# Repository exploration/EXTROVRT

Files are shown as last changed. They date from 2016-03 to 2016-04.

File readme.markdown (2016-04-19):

# EXTROVRT
([EXplo](http://www.explo.org) Telepresence RObot Via the inteRneT)

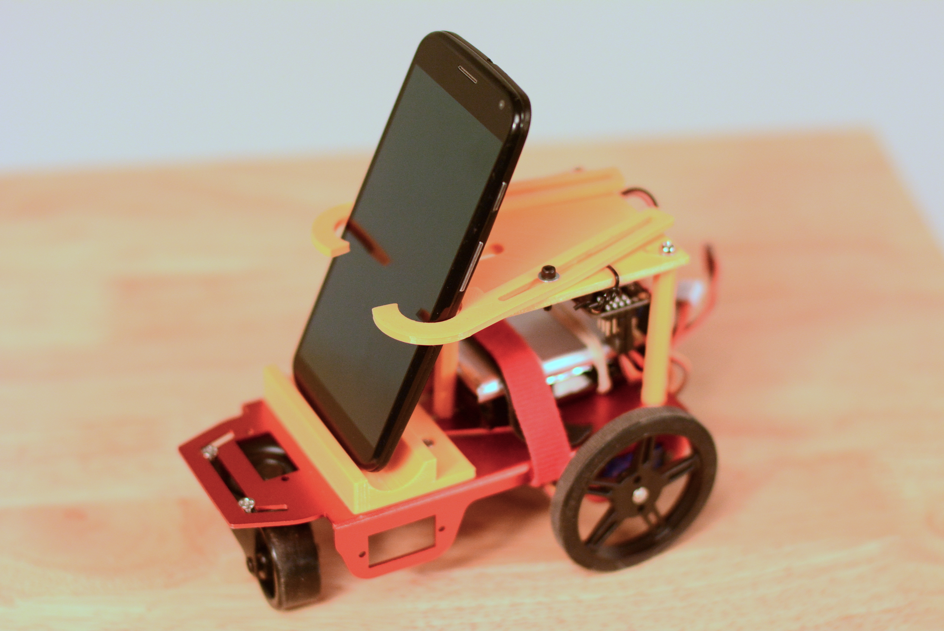
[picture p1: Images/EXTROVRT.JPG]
Glamour shot of the EXTROVRT robot


(more photos in the [Images](Images/) directory)

## What Is It?
EXTROVRT is a telepresence robot controlled via [Adafruit IO](http://adafruit.io)'s MQTT service, which uses [Adafruit Feather](https://www.adafruit.com/categories/777) stuff: the [Feather Huzzah ESP8266](https://www.adafruit.com/products/2821) and [Servo Featherwing](https://www.adafruit.com/products/2928) as the main control boards. We also have a [custom control interface](https://github.com/exploration/EXTROVRT-Control) written in Sinatra which lets us use the keyboard to drive instead of the mouse.

EXTROVRT came about because we have a [Double Robot](http://www.doublerobotics.com/) which was given to us, which we love and is a real hoot. However, it was going to require a brand-new iPad to upgrade. We figured that we could achieve 90% of the functionality of a Double for about 5% of the cost. We set the goal of a robot that could drive around using commodity servo hardware, and hold a phone, iPod touch, iPad, or the like. This would allow us to "turn our head" in virtual meetings, and even drive around a bit, probably mostly on tables.

We've achieved our goal! You should be able to make this robot for about $100, give or take.

This approach also has the benefit of allowing us to use whichever phone/tablet, and whichever video chat client (Skype, Google Hangouts, HipChat Video, etc) works best at the moment. We can also more easily test accessories like camera lenses or microphones.

## How Does It Work?
**Note:** If you want multiple EXTROVRTs, you might want to check out our [control software](https://github.com/exploration/EXTROVRT-Control) for more detailed setup instructions to make that work.

If you just want one robot, you can pretty easily set up the Adafruit IO interface. The way that works is this: You [set up a feed](https://learn.adafruit.com/adafruit-io-basics-feeds/overview) on [Adafruit IO](http://adafruit.io) as such:

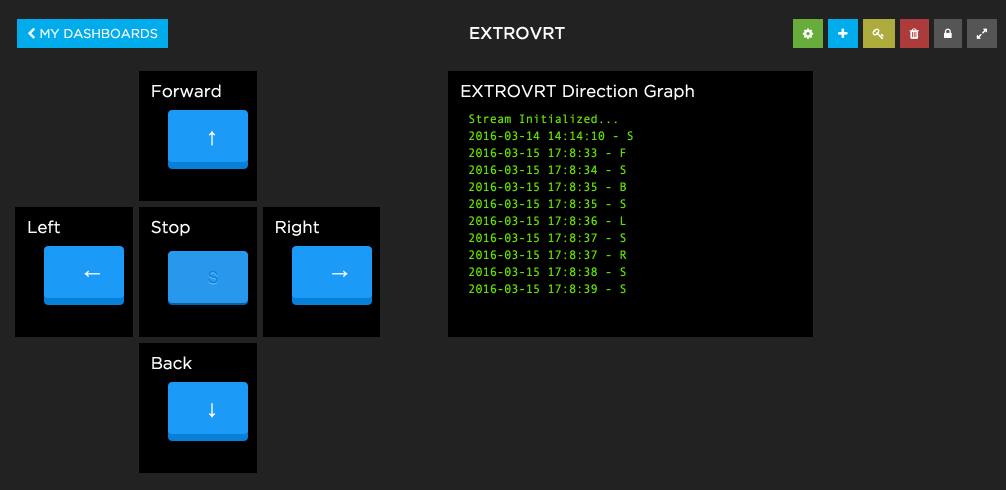
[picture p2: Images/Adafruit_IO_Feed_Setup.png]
Adafruit IO Feed Setup - Buttons with "F","B","L","R", and "S" values


Each button then gets mapped to a simple value: `F` for `Forward`, `B` for `Back`, `R` for `Right`, `L` for `Left`, and `S` for `Stop`. Each button is set up to send `S` when it is let go:

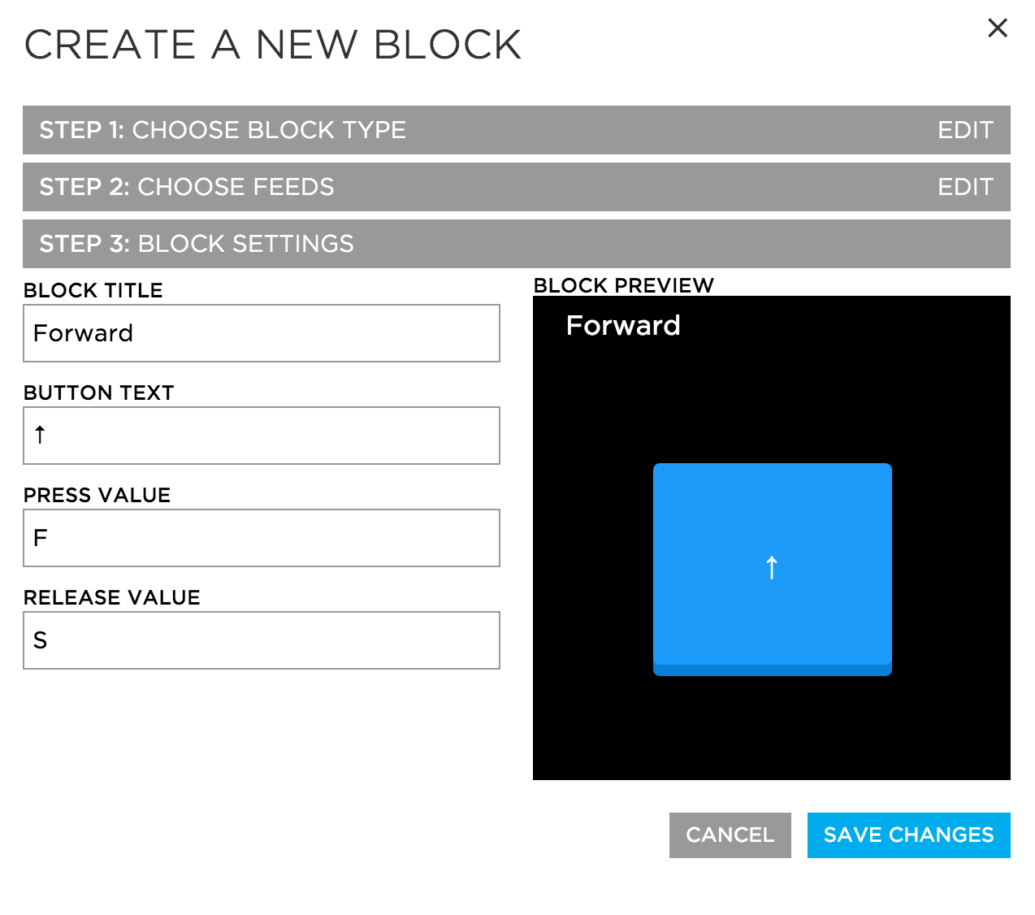
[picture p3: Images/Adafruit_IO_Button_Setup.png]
Adafruit IO Button Setup


For your initial setup, you may want to tweak the motor parameters so that max/min speed correspond to the "threshold" points of your servo motors. In that case, you should put in a "text" block so you can send the `MINUP`,`MINDOWN`,`MAXUP`,`MAXDOWN`,`STOPUP`, and `STOPDOWN` commands to the device. Make sure to record the motor values that work for you and hard-code them into the sketch so you won't have to adjust them every time you reset the device!

The Huzzah ESP8266 board will connect to your wifi, then connect to your Adafruit IO feed using [MQTT](https://learn.adafruit.com/mqtt-adafruit-io-and-you/overview). It monitors the feed for changes in direction, and sends motor information to the servos through the servo board. In practice, this all happens very darned close to real-time: close enough to work great! Until you hit the Adafruit IO API limit :/ But for the price of free, who's complaining?

## How Do I Build It?
### Parts + Assembly
You can get all of the parts for EXTROVRT at this [wishlist](https://www.adafruit.com/wishlists?wid=391765) here.

Physically, the entire robot is built around [this anodyzed aluminum chassis](https://www.adafruit.com/products/2943), two continuous-rotation micro servos with matching wheels, and a swivel-wheel for the front. The parts that hold the phone/tablet are all 3d-printed and bolted on (see below for details).

### Power
You need a battery source that's 5V and capable of handling something in the range of 500mA of current at 5V - 2.5 watts of power. The easiest way to accomplish this is to use a simple [USB Battery Pack](https://www.adafruit.com/products/1959) such as you might use for charging a phone, plugged right into the Feather Huzzah! You'll need to connect the `USB` and `GND` pins to the `+` and `-` screw terminals from the Adafruit Servo Wing to forward the power from USB to the servos (see power draw notes below).

You could alternately use an RC LiPo battery, or a simple 4xAA battery holder - anything is fine, but for this to work you'll have to connect a [UBEC](https://www.adafruit.com/products/1385) (buck converter) to the `USB` and `GND` pins on the Adafruit Feather, as well as the `+` and `-` pins from the Adafruit Servo Wing (the screw terminals) to get a stable 5 volt power source for the devices. Then connect your battery configuration to the other end of the UBEC.

(As an aside about power draw, my testing showed that the Huzzah draws about a continuous 0.05A or 50mA while idle, and the servos both running (normal speed) draws about 0.35A or 350mA. I imagine even if you maxed out the speed of these mini-servos, you'd still be within the 500mA spec of USB, let alone the spec of what a 7.2V 2S RC LiPo battery could attain.)

On my particular robot, I opted for a 2S (~7.3V) LiPo battery instead of the 4xAA holder, but that's only because I have those batteries (and and UBEC, and chargers) lying about from other projects. If you have RC batteries, you may prefer to use those, but most people will probably be happiest with just using a USB battery pack, since those are the most re-usable for other purposes when you're not EXTROVRT'ing.

### Wiring
Electronics-wise, you plug the servo "wing" on top of the Feather Huzzah! As noted above, you want to connect the `USB` and `GND` pins on the Adafruit Feather to the `+` and `-` pins from the Adafruit Servo Wing (the screw terminals) (and also to the 5V output of the UBEC if you're using one). On my devices, I install a power switch between the UBEC and the electronics so that I don't have to unplug any cables to turn the thing on + off.

### Arduino
The Arduino files are in the `Arduino` folder of this repository. You simply have to modify them to match your WiFi network SSID/password, and your particular Adafruit IO feed information. If you don't know how to upload Arduino code to the board, [this tutorial](https://learn.adafruit.com/adafruit-feather-huzzah-esp8266/overview) is exceedingly helpful.

### 3D Printing
Everything that's orange in the pictures is a 3d-printed thing. You'll need to print your own copy of those. You want two of the "arms", one top plate, and one base.

The CAD sources for the 3D-printed files are publicly available at [OnShape](https://cad.onshape.com/documents/d73cca1ae031f4b278264cff/w/0abe2b13ef53c6019a28a62a), which is handy if you want to fiddle with the models for your own setup.

I've also included the STL models and the [Simplify3D](https://www.simplify3d.com/) print setup files for a [PrintrBot Simple Metal](http://printrbot.com/shop/assembled-simple-metal/) in the `Models` and `Print Setup` folders, if you've got the same setup as me or use Simplify3D and want a starting point. I was able to print the entire thing within one 150mm square build plate.

I also had some luck making my own 3d-printed [Hex Standoffs](https://cad.onshape.com/documents/a721d24ec3e00633c0a5e028/w/56f9fc784b3159de2bad2fdf/e/3c67c912763ba927c46253c3), which is one fewer part you have to purchase if you have your own printer. Yes, I used imperial bolts (4/40) for that particular one, because I ran out of nice metric ones. But they should work with M3 bolts as well. And once again, it's OnShape, so it's easy to go + change dimensions and make your own - the model is fully parametric. You should be able to print them sideways on your build plate - it worked fine for me with no supports.

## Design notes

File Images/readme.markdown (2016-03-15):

Front
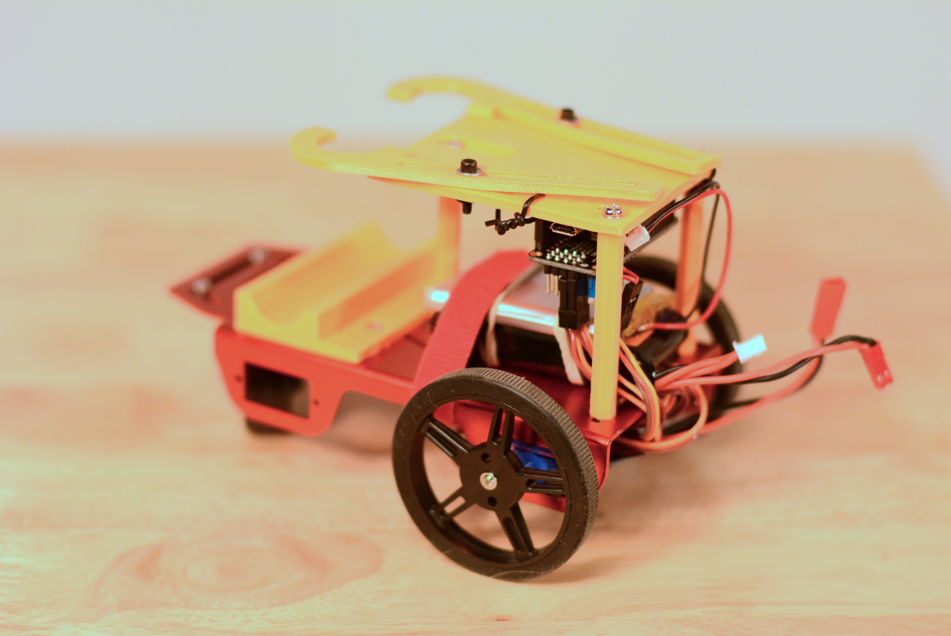
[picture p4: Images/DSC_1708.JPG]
Back Left Corner View

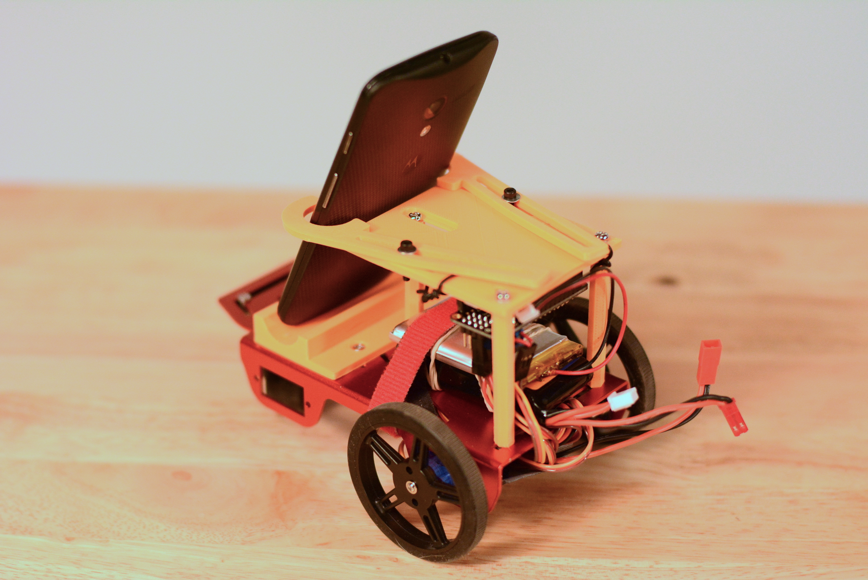
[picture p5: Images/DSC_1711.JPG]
Back Left with Phone View

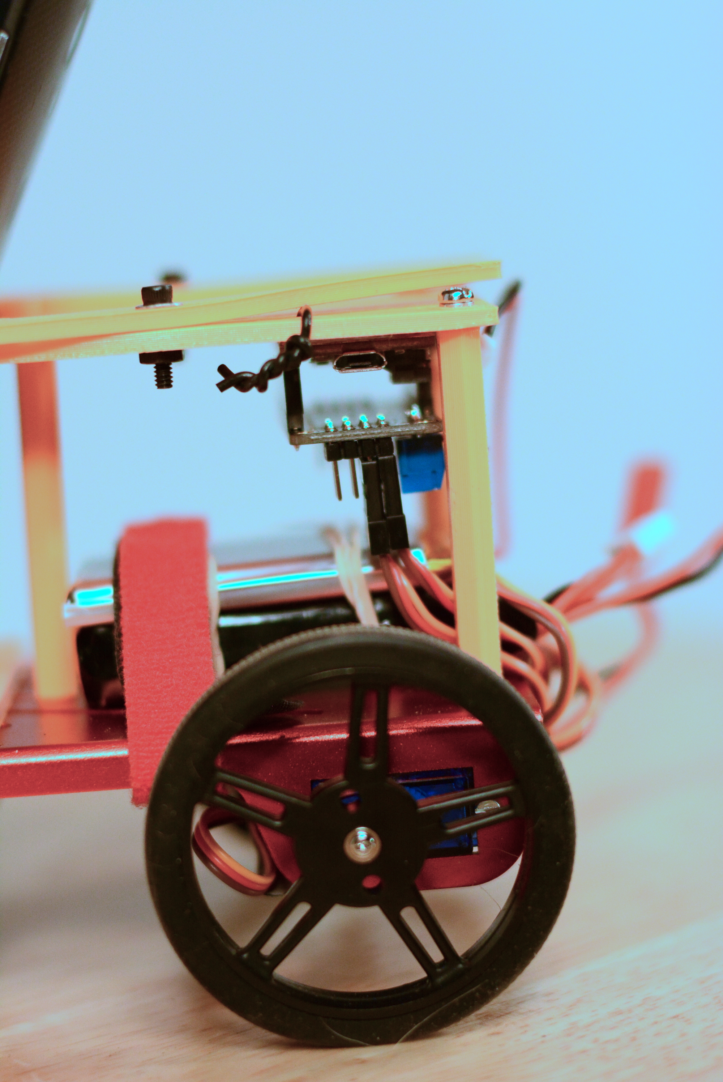
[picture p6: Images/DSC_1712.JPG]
Electronics Detail

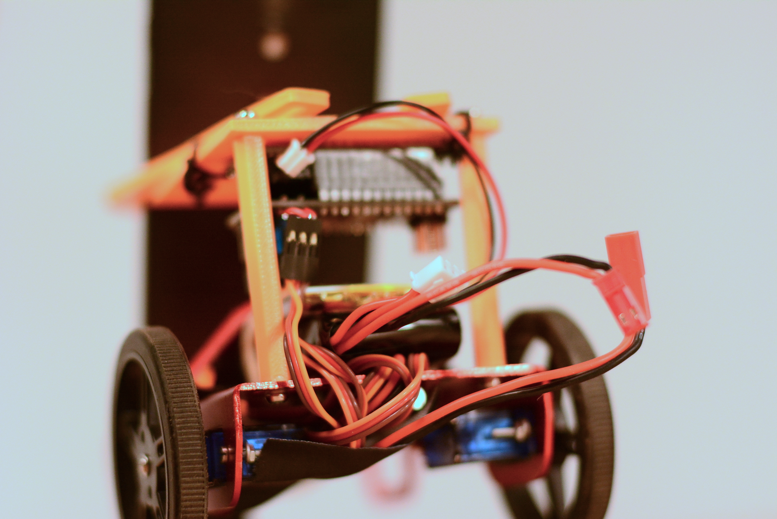
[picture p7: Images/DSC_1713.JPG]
Rear View

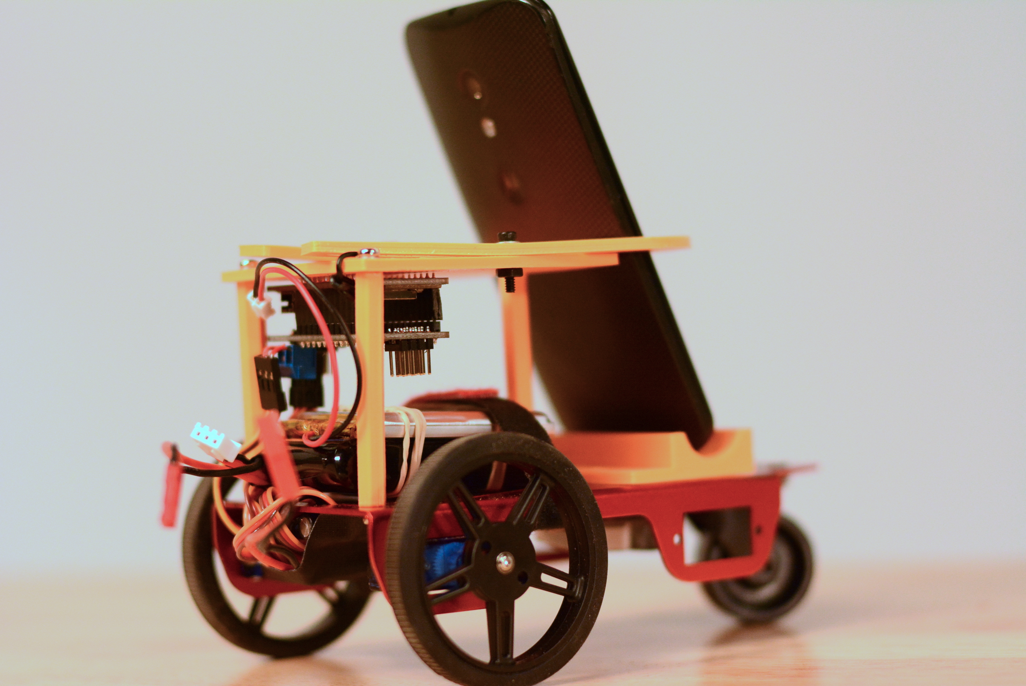
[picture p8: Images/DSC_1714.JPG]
Back Right View

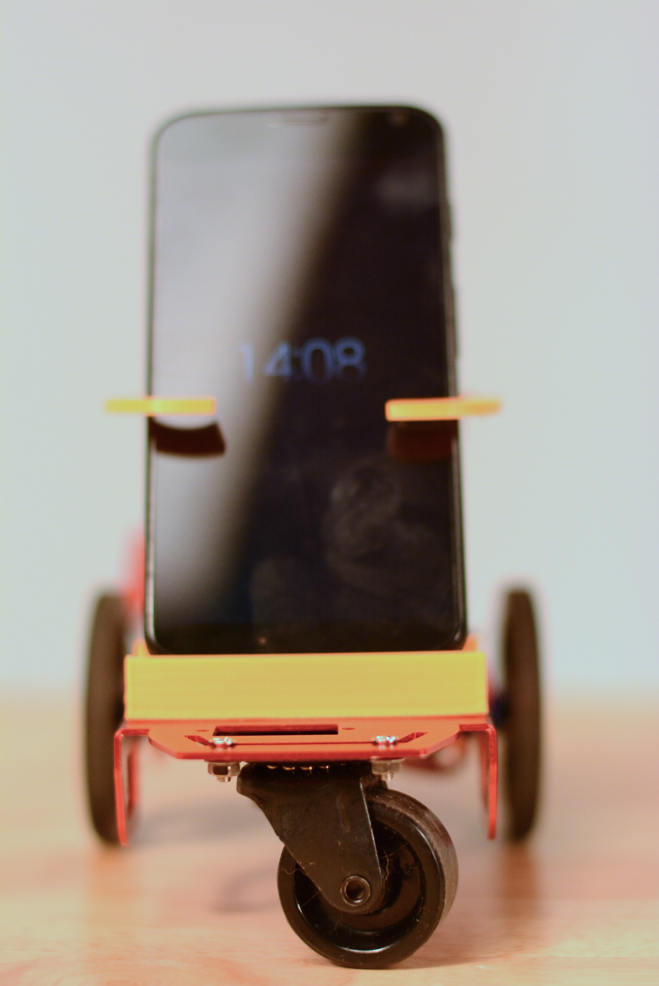
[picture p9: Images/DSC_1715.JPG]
Front View

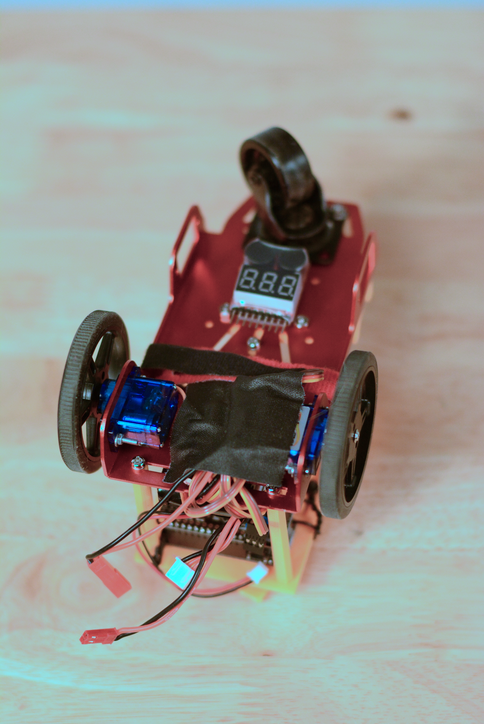
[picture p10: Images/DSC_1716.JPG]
Bottom View


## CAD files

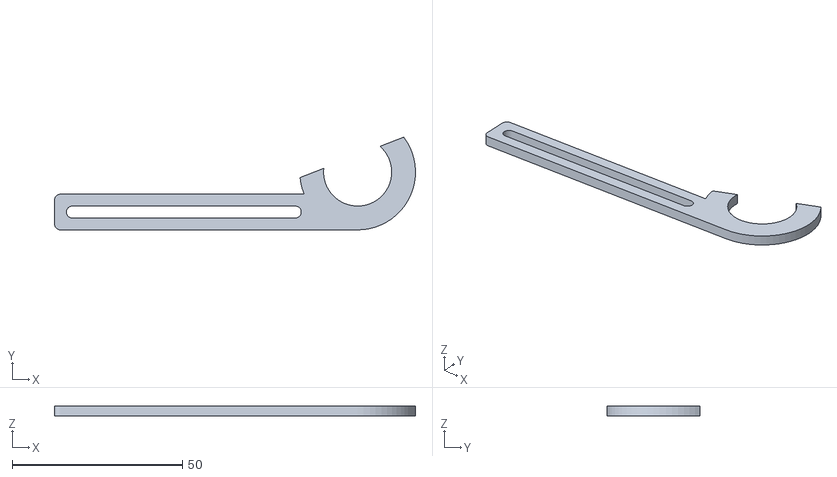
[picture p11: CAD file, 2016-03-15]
Models/iOS Device Robot Mount v2 - Arm.stl
106.1 x 27.3 x 3.00

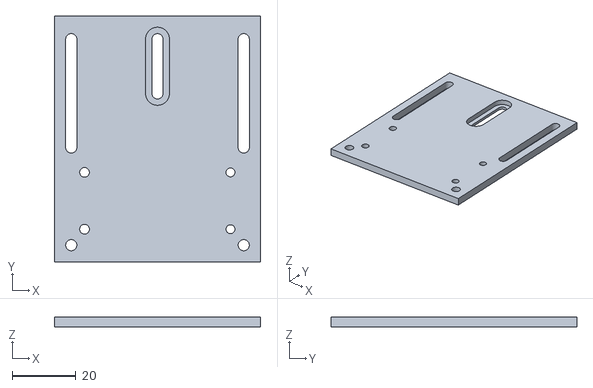
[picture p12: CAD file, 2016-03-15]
Models/iOS Device Robot Mount v2 - Top Plate.stl
64.5 x 77.0 x 3.00

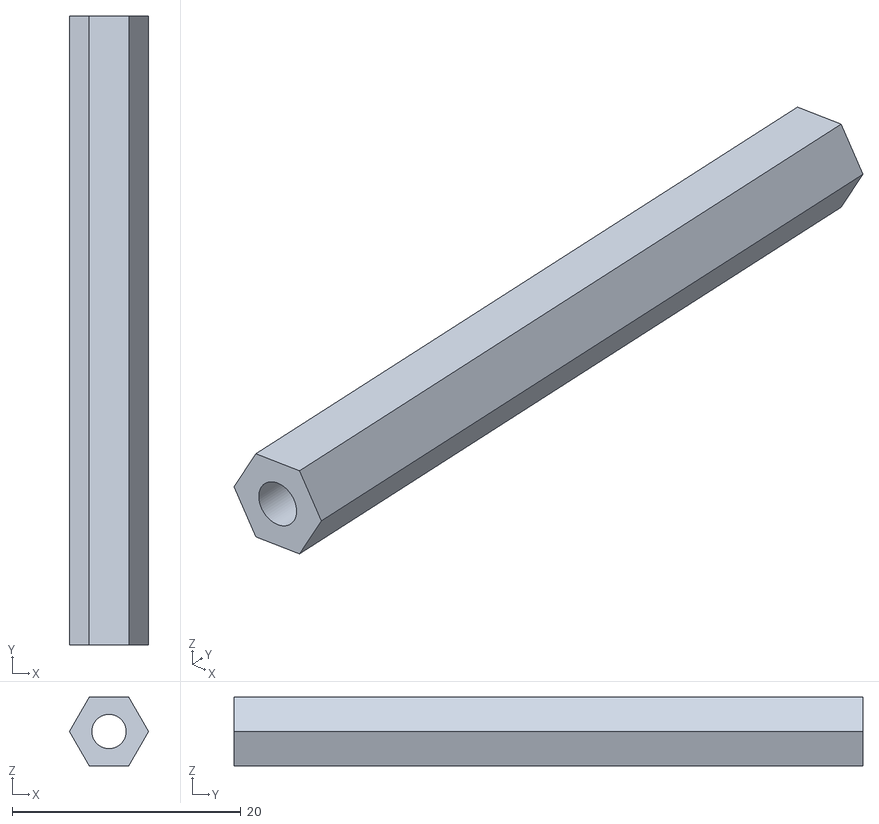
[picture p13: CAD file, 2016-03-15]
Models/Hex Standoff - 4-40 x 1-.stl
6.93 x 55.0 x 6.00

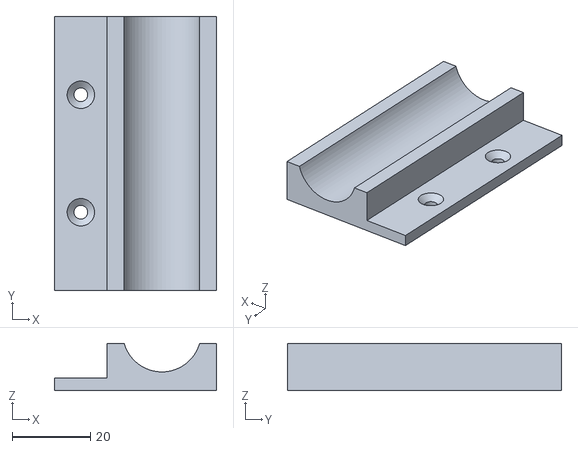
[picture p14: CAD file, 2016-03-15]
Models/iOS Device Robot Mount v2 - Floor Plate.stl
41.4 x 70.0 x 12.0

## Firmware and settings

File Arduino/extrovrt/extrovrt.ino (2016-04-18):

//wifi stuff
#include <ESP8266WiFi.h>
#include "Adafruit_MQTT.h"
#include "Adafruit_MQTT_Client.h"
//servo stuff
#include <Wire.h>
#include <Adafruit_PWMServoDriver.h>

/************************* WiFi Access Point *********************************/

#define WLAN_SSID       "YOUR_WIFI_SSID"
#define WLAN_PASS       "YOUR_WIFI_PASSWORD"

/************************* Adafruit.io Setup *********************************/

#define AIO_SERVER      "io.adafruit.com"
#define AIO_SERVERPORT  1883
#define AIO_USERNAME    "YOUR_AIO_USERNAME"
#define AIO_KEY         "YOUR_AIO_KEY"


/************ Global State (you don't need to change this!) ******************/

// Create an ESP8266 WiFiClient class to connect to the MQTT server.
WiFiClient client;

// Store the MQTT server, client ID, username, and password in flash memory.
// This is required for using the Adafruit MQTT library.
const char MQTT_SERVER[] PROGMEM    = AIO_SERVER;
// Set a unique MQTT client ID using the AIO key + the date and time the sketch
// was compiled (so this should be unique across multiple devices for a user,
// alternatively you can manually set this to a GUID or other random value).
const char MQTT_CLIENTID[] PROGMEM  = __TIME__ AIO_USERNAME;
const char MQTT_USERNAME[] PROGMEM  = AIO_USERNAME;
const char MQTT_PASSWORD[] PROGMEM  = AIO_KEY;

// Setup the MQTT client class by passing in the WiFi client and MQTT server and login details.
Adafruit_MQTT_Client mqtt(&client, MQTT_SERVER, AIO_SERVERPORT, MQTT_CLIENTID, MQTT_USERNAME, MQTT_PASSWORD);


/****************************** Feeds ***************************************/
// Setup a feed called 'extrovrt-direction' for subscribing to changes.
const char EV_FEED[] PROGMEM = AIO_USERNAME "/feeds/extrovrt-direction";
Adafruit_MQTT_Subscribe extrovrt_direction = Adafruit_MQTT_Subscribe(&mqtt, EV_FEED);


/****************************** Servo ***************************************/
// Called this way, it uses the default address 0x40
Adafruit_PWMServoDriver pwm = Adafruit_PWMServoDriver();
// We are using continuous rotation servos, so in this case "minimum" is fully
// backwards, "maximum" is fully forwards, and "stop" is the middle inflection
// point
// NOTE: Plan on tweaking these up or down with your particular set of motors 
//       until it works
// 339 is bare-minimum (slowest)
int MOTORMIN = 332;
// this is the "inflection point" on a CR servo where it stops in the middle
int MOTORSTOP = 355;
// 362 is bare-maximum (slowest)
int MOTORMAX = 366;
#define LEFTSERVO 0
#define RIGHTSERVO 1


/*************************** Sketch Code ************************************/

// Bug workaround for Arduino 1.6.6, it seems to need a function declaration
// for some reason (only affects ESP8266, likely an arduino-builder bug).
void MQTT_connect();
void moveWheels(uint16_t left, uint16_t right);

void setup() {
  Serial.begin(115200);

  // Setup servo
  pwm.begin();
  pwm.setPWMFreq(60);  // Analog servos run at ~60 Hz updates
  moveWheels(MOTORSTOP, MOTORSTOP);
  yield();
  
  // Connect to WiFi access point.
  Serial.println(); Serial.println();
  Serial.print("Connecting to ");
  Serial.println(WLAN_SSID);

  WiFi.begin(WLAN_SSID, WLAN_PASS);
  while (WiFi.status() != WL_CONNECTED) {
    delay(500);
    Serial.print(".");
  }
  Serial.println();

  Serial.println("WiFi connected");
  Serial.println("IP address: "); Serial.println(WiFi.localIP());

  // Setup MQTT subscription for onoff feed.
  mqtt.subscribe(&extrovrt_direction);

}

/*
 * test loop
void loop() {
  moveWheels(MOTORMIN,MOTORMIN);
  delay(1000);
  moveWheels(MOTORSTOP,MOTORSTOP);
  delay(1000);
  moveWheels(MOTORMAX,MOTORMAX);
  delay(1000);
  moveWheels(MOTORSTOP,MOTORSTOP);
  delay(1000);
}
*/


void loop() {
  // Ensure the connection to the MQTT server is alive (this will make the first
  // connection and automatically reconnect when disconnected).  See the MQTT_connect
  // function definition further below.
  MQTT_connect();

  // this is our 'wait for incoming subscription packets' busy subloop
  Adafruit_MQTT_Subscribe *subscription;
  while ((subscription = mqtt.readSubscription(1000))) {
    if (subscription == &extrovrt_direction) {
      Serial.print (F("Got: "));
      Serial.println((char *)extrovrt_direction.lastread);

      // check directions
      if (0 == strcmp((char *)extrovrt_direction.lastread, "F")) {
        Serial.println("Moving Forward");
        moveWheels(MOTORMAX, MOTORMAX);
      } else if (0 == strcmp((char *)extrovrt_direction.lastread, "B")) {
        Serial.println("Moving Backward");
        moveWheels(MOTORMIN, MOTORMIN);
      } else if (0 == strcmp((char *)extrovrt_direction.lastread, "R")) {
        Serial.println("Moving Right");
        moveWheels(MOTORMAX, MOTORMIN);
      } else if (0 == strcmp((char *)extrovrt_direction.lastread, "L")) {
        Serial.println("Moving Left");
        moveWheels(MOTORMIN, MOTORMAX);
      } else if (0 == strcmp((char *)extrovrt_direction.lastread, "S")) {
        Serial.println("Stopping");
        moveWheels(MOTORSTOP, MOTORSTOP);
      } else if (0 == strcmp((char *)extrovrt_direction.lastread, "MAXUP")) {
        MOTORMAX += 1;
        Serial.print("Increasing top speed to ");
        Serial.println(MOTORMAX);
      } else if (0 == strcmp((char *)extrovrt_direction.lastread, "MAXDOWN")) {
        MOTORMAX -= 1;
        Serial.print("Decreasing top speed to ");
        Serial.println(MOTORMAX);
      } else if (0 == strcmp((char *)extrovrt_direction.lastread, "MINUP")) {
        MOTORMIN += 1;
        Serial.print("Increasing min speed to ");
        Serial.println(MOTORMIN);
      } else if (0 == strcmp((char *)extrovrt_direction.lastread, "MINDOWN")) {
        MOTORMIN -= 1;
        Serial.print("Decreasing min speed to ");
        Serial.println(MOTORMIN);
      } else if (0 == strcmp((char *)extrovrt_direction.lastread, "STOPUP")) {
        MOTORSTOP += 1;
        Serial.print("Increasing motor stop to ");
        Serial.println(MOTORSTOP);
      } else if (0 == strcmp((char *)extrovrt_direction.lastread, "STOPDOWN")) {
        MOTORSTOP -= 1;
        Serial.print("Decreasing motor stop to ");
        Serial.println(MOTORSTOP);
      }
    } 
  }

  delay(1000);
}


// send this the PWM values you want for each wheel + it'll handle the movement
// it will also handle the fact that the right wheel has its direction reversed
void moveWheels(uint16_t left, uint16_t right) {
  // reverse the right motor
  if (right == MOTORMIN) { right = MOTORMAX; }
  else if (right == MOTORMAX) { right = MOTORMIN; }
  
  Serial.print("Left: ");
  Serial.println(left);
  Serial.print("Right: ");
  Serial.println(right);
  pwm.setPWM(LEFTSERVO, 0,  left);
  pwm.setPWM(RIGHTSERVO, 0, right);
}

// Function to connect and reconnect as necessary to the MQTT server.
// Should be called in the loop function and it will take care if connecting.
void MQTT_connect() {
  int8_t ret;

  // Stop if already connected.
  if (mqtt.connected()) {
    return;
  }

  Serial.print("Connecting to MQTT... ");

  while ((ret = mqtt.connect()) != 0) { // connect will return 0 for connected
       Serial.println(mqtt.connectErrorString(ret));
       Serial.println("Retrying MQTT connection in 5 seconds...");
       mqtt.disconnect();
       delay(5000);  // wait 5 seconds
  }
  Serial.println("MQTT Connected!");
}

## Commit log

2016-03-15 clarify volts
2016-03-15 3d printing clarification
2016-04-18 add ability to tweak motor params via software
2016-04-18 you only need one battery pack! much simpler.
2016-04-18 add notes about power draw measurements
2016-04-19 update to point out that USB battery pack is best power option
